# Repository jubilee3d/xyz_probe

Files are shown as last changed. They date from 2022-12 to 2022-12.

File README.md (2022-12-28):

# Jubilee XYZ Probe Tool
A touch probe for various measurement applications

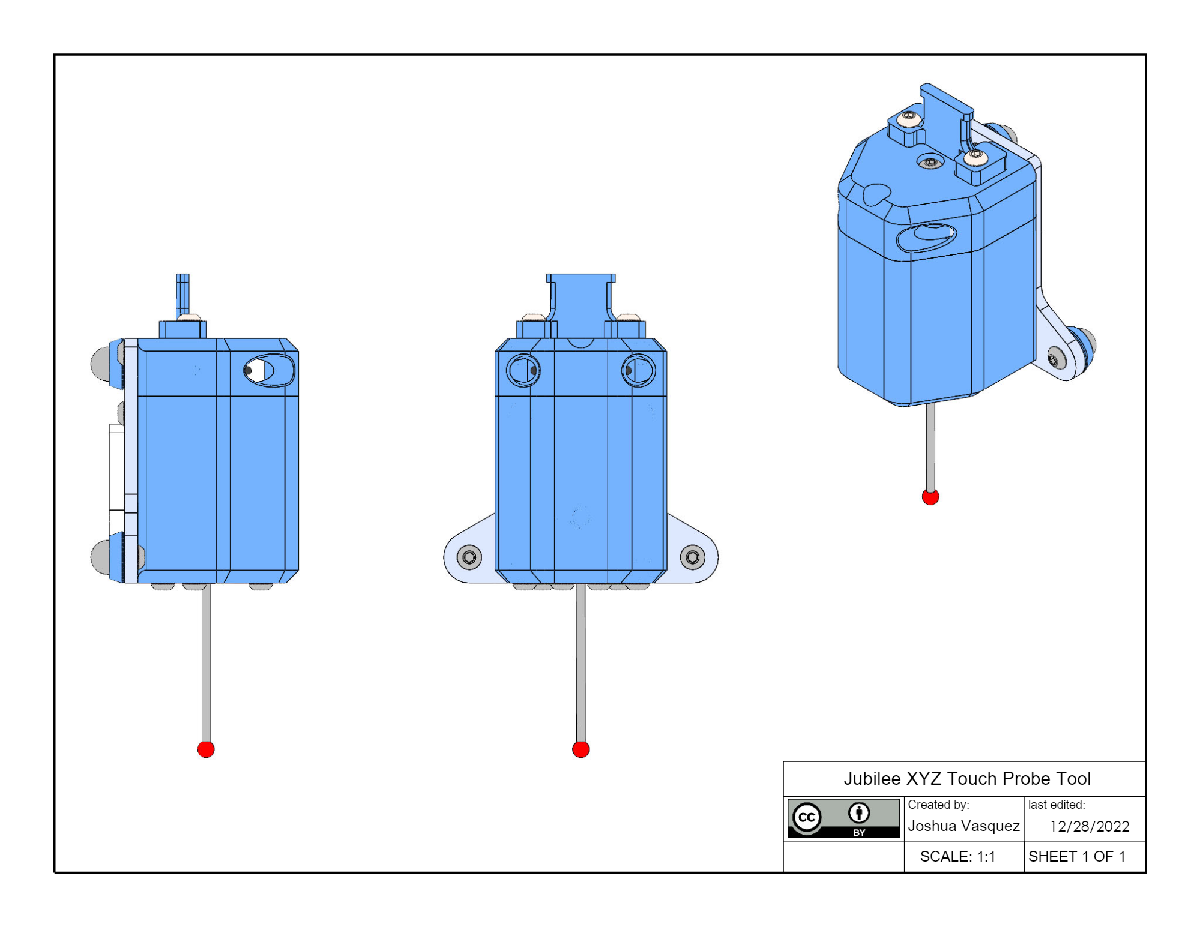
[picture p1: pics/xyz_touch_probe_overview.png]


## Overview
This is a Jubilee-compatible XYZ Probe.
It can act as a replacement for the existing z-limit switch or as a general means of inspecting items on the bed.
Probing gives the machine the ability to register against arbitrary features on the bed, enabling the possibility of resuming partial prints, scanning objects, or inspecting the existing dimensions of objects.

The XYZ probe can be reproduced from both printed and stock parts with a single unit costing about $50.
Simply order the parts in the [Shopping List](https://docs.google.com/spreadsheets/d/1exzQQtGWq62kmWazMUU2xbrfU62XK9QZYXhOB--K8R0/edit?usp=sharing) and follow the step-by-step instructions.

For more information on provisioning this tool for Jubilee, have a look at its corresponding [tool page](https://jubilee3d.com/index.php?title=XYZ_Probe_Tool).

## Specs
* probe the full XY volume. Probe *into* pockets up to 38 [mm] deep.
* compact! Does not sacrifice any of the build volume.
* Purchased Parts called out in the [Shopping List]()

## Community
This tool is part of the bigger ecosystem of Jubilee-compatible tools that implement the [E3D Toolchanger Coupler](https://github.com/e3donline/ToolChanger) standard.
For more on Jubilee, have a look at the [parent project](https://github.com/machineagency/jubilee) or join the [Discord](https://discord.gg/jubilee).

## Who made this?
This tool was created by [Joshua Vasquez](http://www.doublejumpelectric.com/) formerly at [Machine Agency](http://depts.washington.edu/machines/) at the University of Washington.

## Use the Source!
This tool is licensed with a [Creative Commons Attribution 4.0 Unported License](https://creativecommons.org/licenses/by/4.0/).

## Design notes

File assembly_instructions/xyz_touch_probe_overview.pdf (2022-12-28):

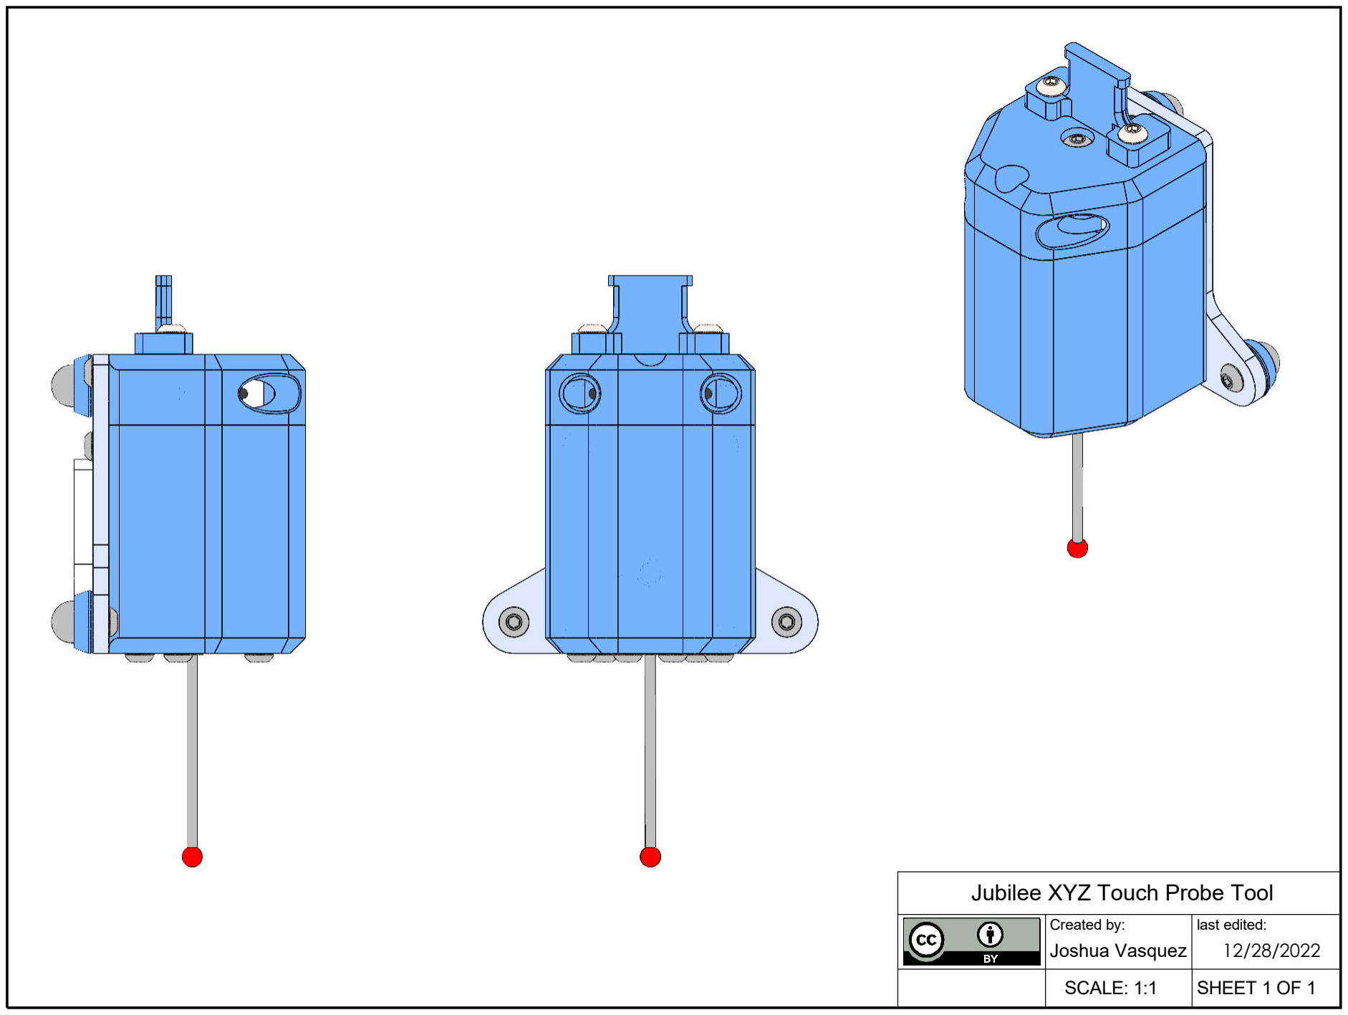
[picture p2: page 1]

12/28/2022

SHEET 1 OF 1

last edited:

SCALE: 1:1

Joshua Vasquez

Created by:

### Jubilee XYZ Touch Probe Tool

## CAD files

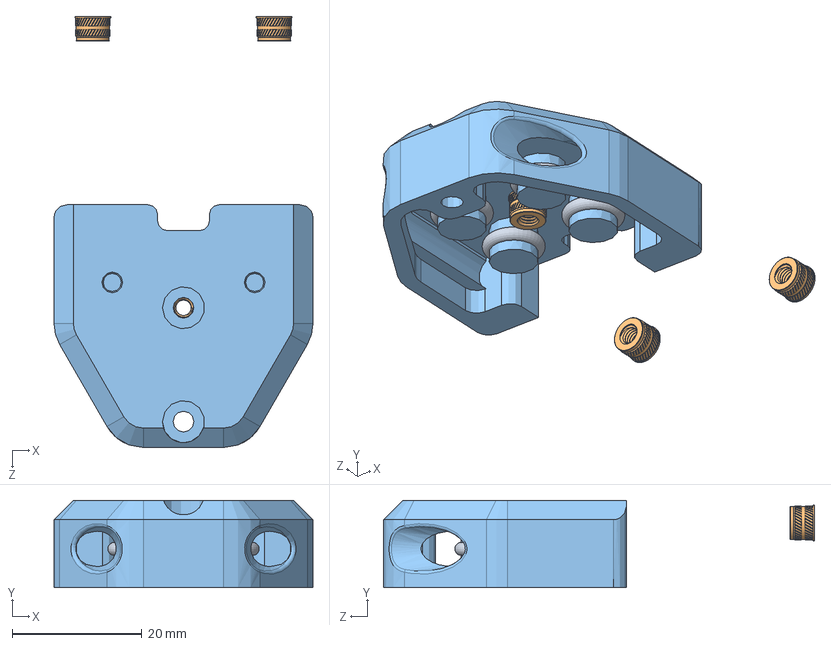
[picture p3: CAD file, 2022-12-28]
cads/solidworks/lid_assembly.SLDASM
40.0 x 13.5 x 66.6 mm
5x9x2_oring x 4
m3_heat_set_insert_94180A331 x 3
housing

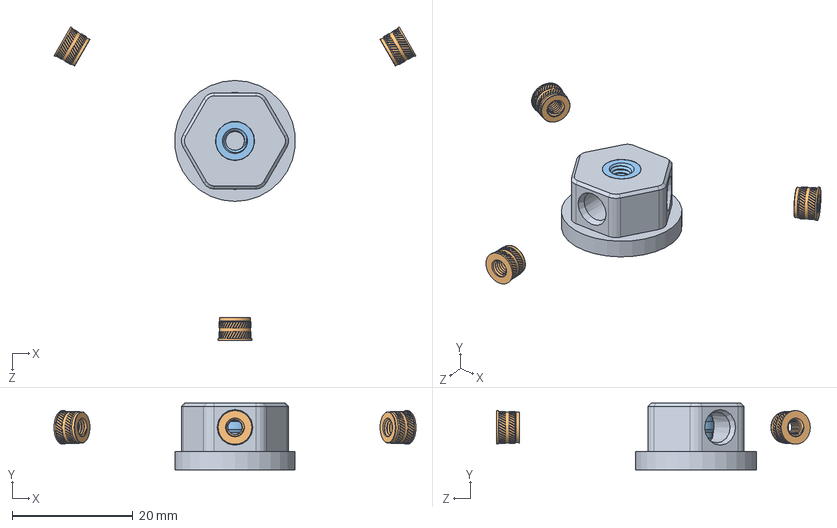
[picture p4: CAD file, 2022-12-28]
cads/solidworks/coupling_junction.SLDASM
59.8 x 11.0 x 51.8 mm
touch_probe_coupling_joint
m3_heat_set_insert_94180A331 x 3
m4_heat_set_insert_long_94180A353

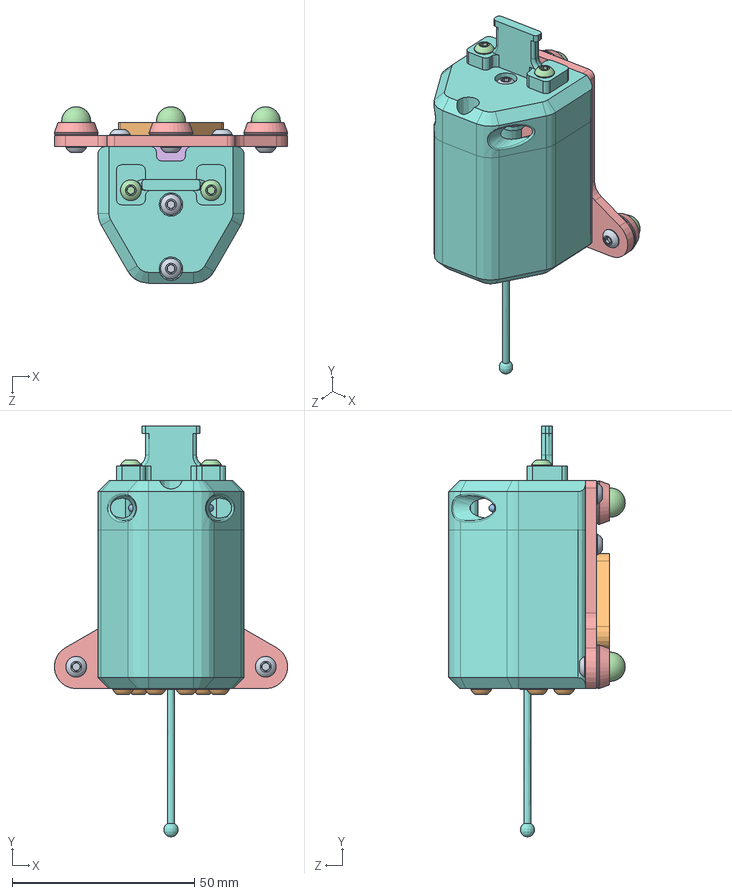
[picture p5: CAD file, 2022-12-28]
cads/solidworks/touch_probe_v2.SLDASM
64.0 x 112.7 x 48.4 mm
m3_6mm_buttonhead_screw_92095A179 x 11
wedge_plate
m3_6mm_flathead_screw_92125A126 x 3
m3_threaded_ball x 3
metal_base_tool_plate x 4
pcb
m3_8mm_threaded_ball x 6
housing x 4
m3_heat_set_insert_94180A331 x 11
m3_12mm_buttohead_screw_92095A183 x 6
5x9x2_oring x 4
m3_8mm_buttonhead_screw_92095A181 x 2
touch_probe_coupling_joint
m4_heat_set_insert_long_94180A353
m3_shoulder_screw_4mm_d_8mm_l_94128A105 x 3
probe

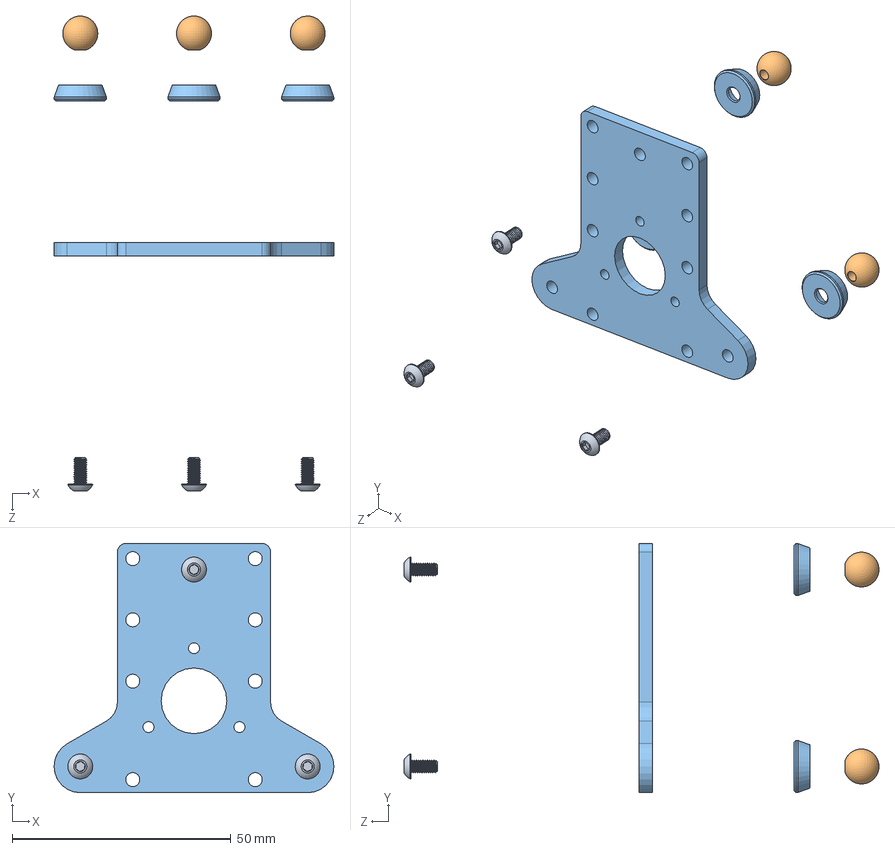
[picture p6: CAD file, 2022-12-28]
cads/solidworks/base_tool_plate_assembly.SLDASM
64.0 x 57.0 x 108.6 mm
m3_6mm_buttonhead_screw_92095A179 x 3
m3_threaded_ball x 3
metal_base_tool_plate x 4

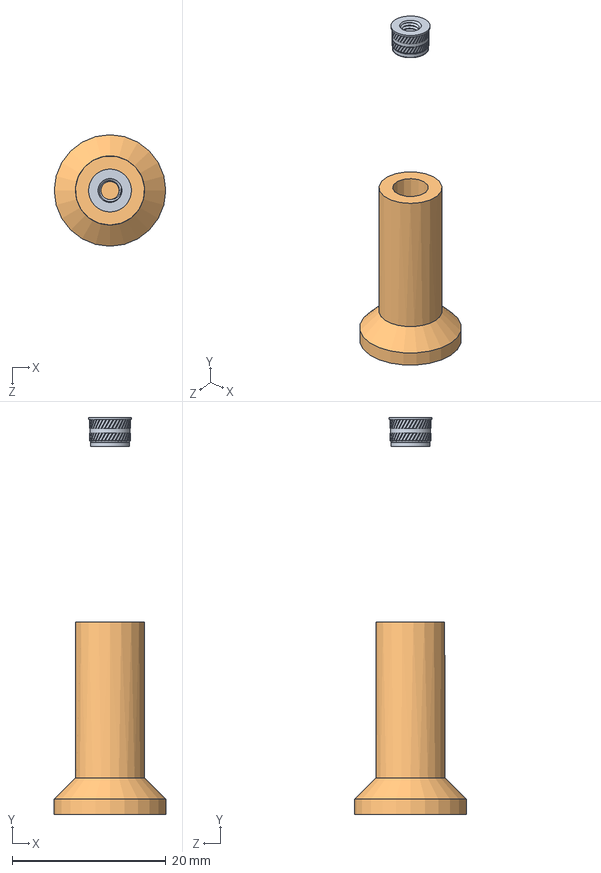
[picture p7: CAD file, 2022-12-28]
cads/solidworks/spring_preload_stud.SLDASM
14.5 x 51.6 x 14.5 mm
m3_heat_set_insert_94180A331
housing

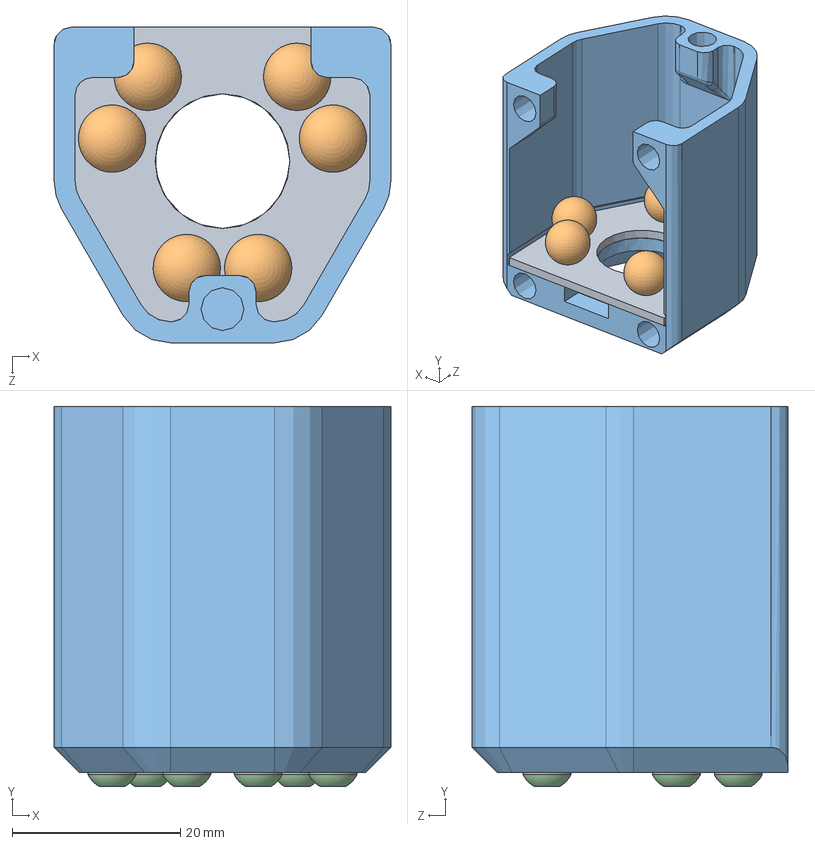
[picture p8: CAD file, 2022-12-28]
cads/solidworks/base_with_tool_balls.SLDASM
40.0 x 45.2 x 37.5 mm
pcb
m3_8mm_threaded_ball x 6
housing
m3_12mm_buttohead_screw_92095A183 x 6

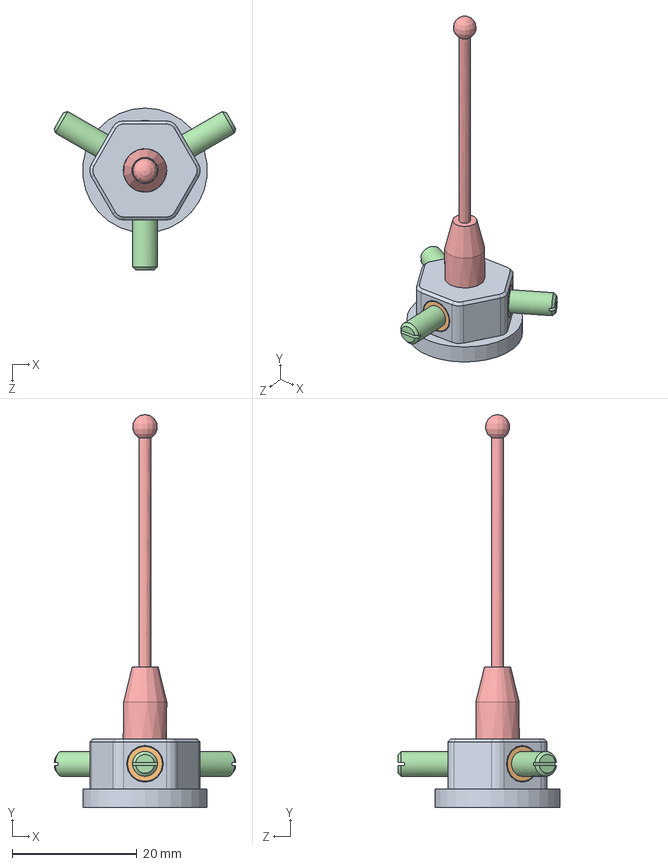
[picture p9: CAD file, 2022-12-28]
cads/solidworks/probe_tip.SLDASM
29.1 x 63.0 x 26.0 mm
touch_probe_coupling_joint
m3_heat_set_insert_94180A331 x 3
m4_heat_set_insert_long_94180A353
m3_shoulder_screw_4mm_d_8mm_l_94128A105 x 3
probe

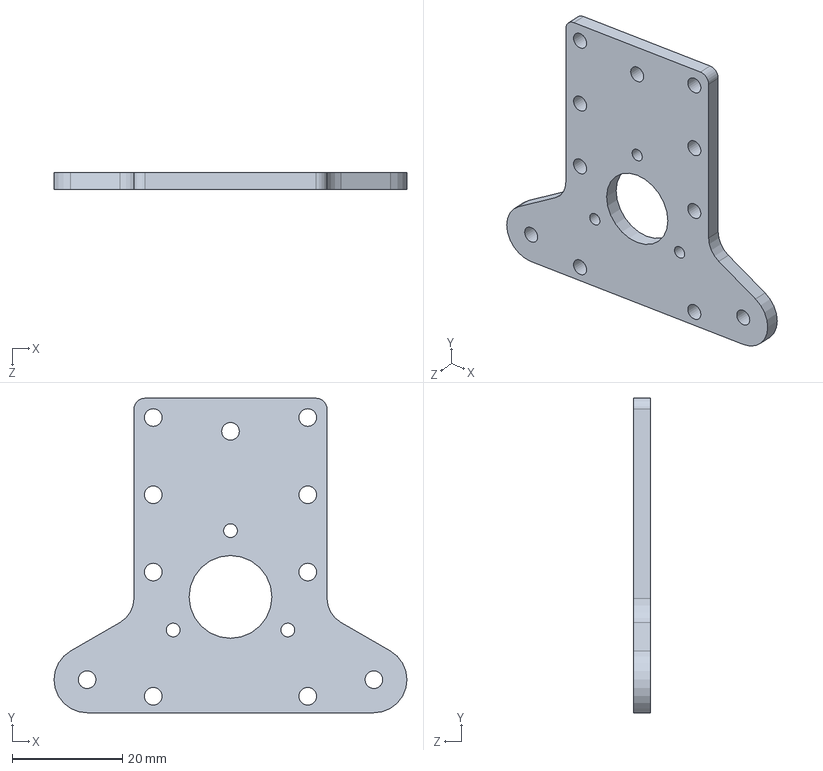
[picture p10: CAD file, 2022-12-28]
cads/solidworks/metal_base_tool_plate.SLDPRT
64.0 x 57.0 x 3.00 mm

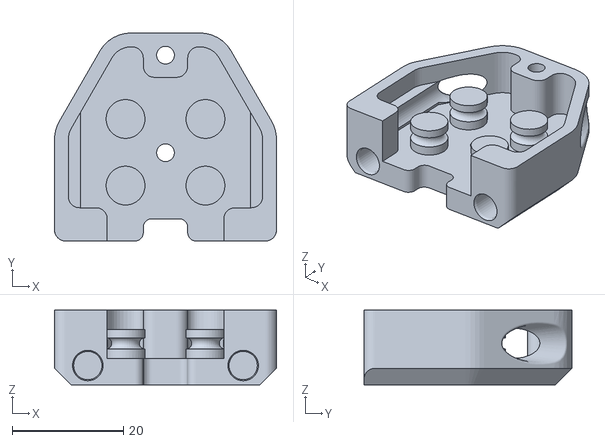
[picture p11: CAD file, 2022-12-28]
fabrication_exports/printed_lid.STL
40.0 x 37.5 x 13.5

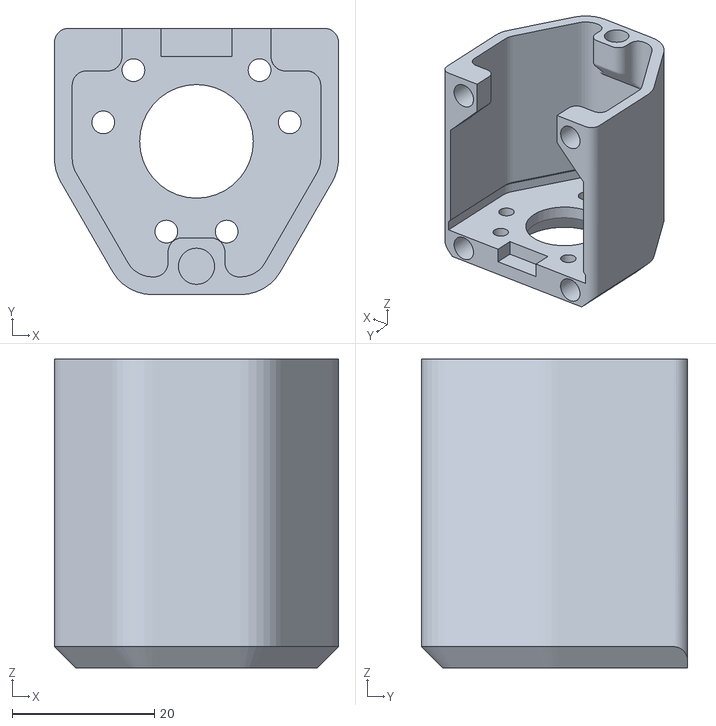
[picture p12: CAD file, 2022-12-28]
fabrication_exports/printed_base.STL
40.0 x 37.5 x 43.5

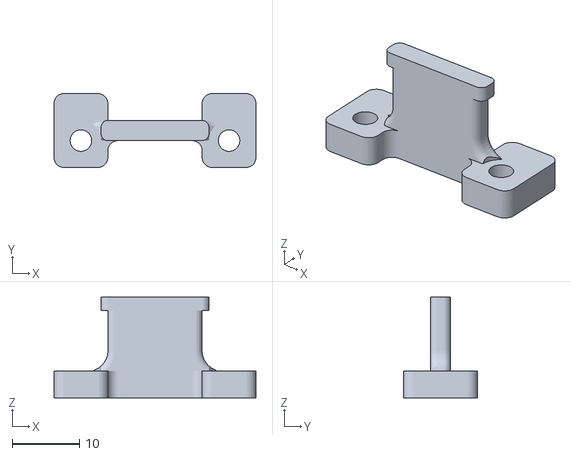
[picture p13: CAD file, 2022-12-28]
fabrication_exports/printed_wire_tab.STL
30.0 x 11.0 x 15.0

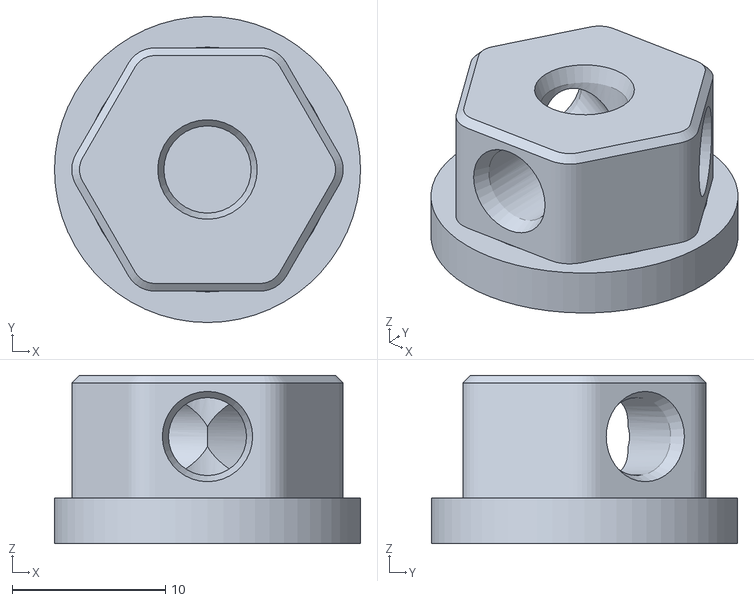
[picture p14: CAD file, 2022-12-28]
fabrication_exports/coupling_junction.STL
20.0 x 20.0 x 11.0

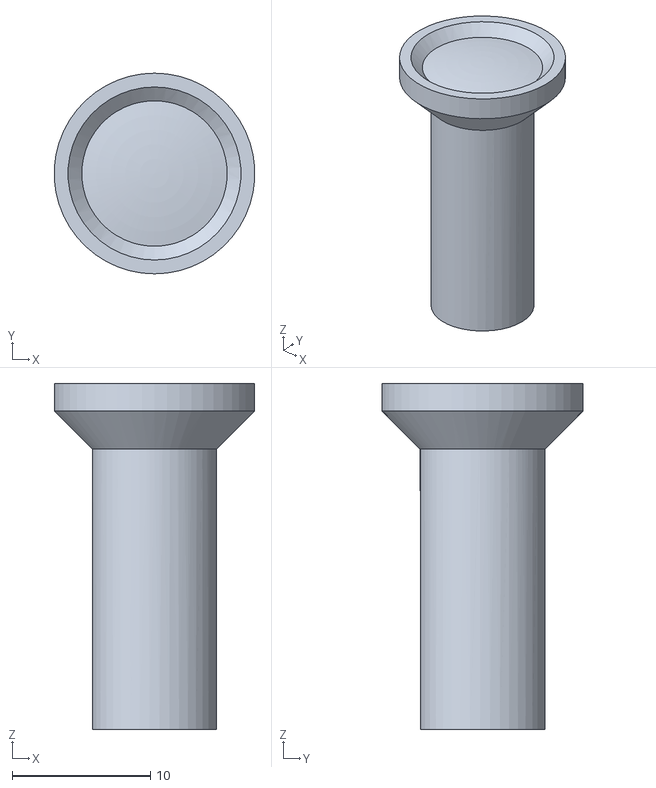
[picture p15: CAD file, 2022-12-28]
fabrication_exports/printed_spring_stud.STL
14.5 x 14.5 x 25.0

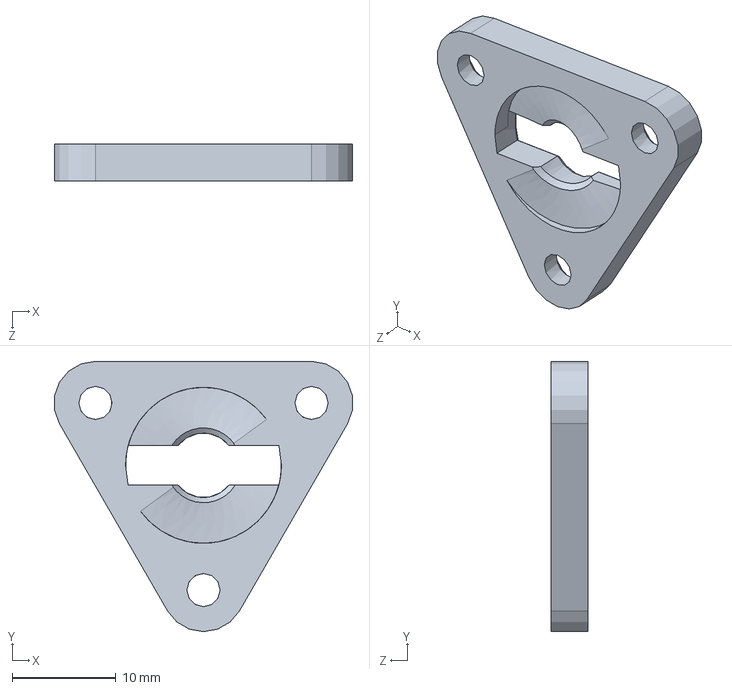
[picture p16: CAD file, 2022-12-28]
cads/solidworks/wedge_plate.SLDPRT
28.7 x 26.0 x 3.60 mm

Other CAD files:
fabrication_exports/tool_ball_cup.STL
cads/solidworks/pcb.SLDPRT
cads/solidworks/m3_threaded_ball.SLDPRT
cads/solidworks/probe.SLDPRT
cads/solidworks/5x9x2_oring.SLDPRT
cads/solidworks/housing.SLDPRT
cads/solidworks/m3_12mm_buttohead_screw_92095A183.SLDPRT
cads/solidworks/m3_6mm_buttonhead_screw_92095A179.SLDPRT
cads/solidworks/m3_6mm_flathead_screw_92125A126.SLDPRT
cads/solidworks/m3_8mm_buttonhead_screw_92095A181.SLDPRT
cads/solidworks/m3_8mm_threaded_ball.SLDPRT
cads/solidworks/m3_heat_set_insert_94180A331.SLDPRT
cads/solidworks/m3_shoulder_screw_4mm_d_8mm_l_94128A105.SLDPRT
cads/solidworks/m4_heat_set_insert_long_94180A353.SLDPRT
cads/solidworks/touch_probe_coupling_joint.SLDPRT

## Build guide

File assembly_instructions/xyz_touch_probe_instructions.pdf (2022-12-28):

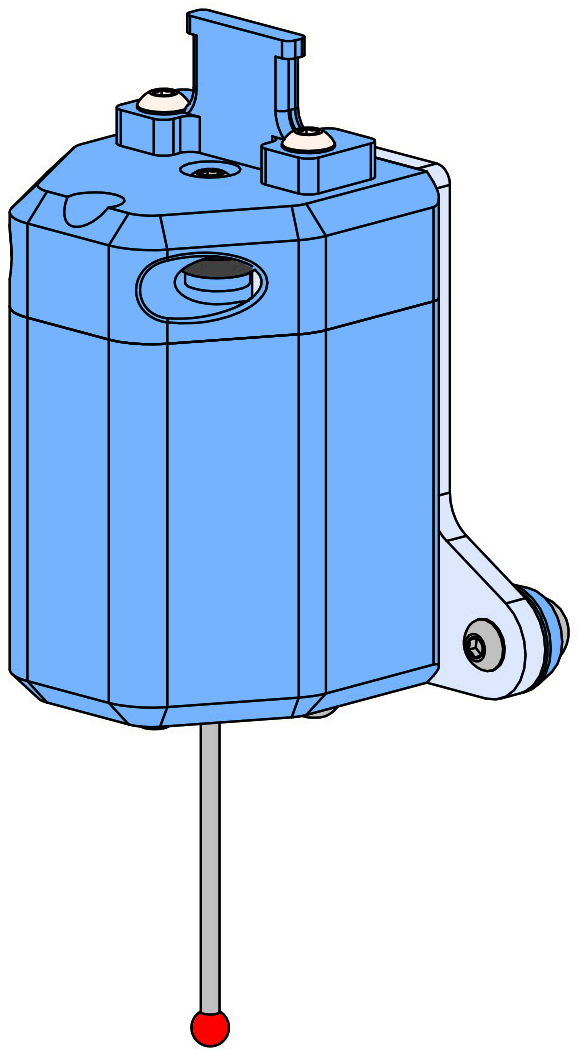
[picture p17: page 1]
SCALE: 1:5; SHEET 1 OF 11; Joshua Vasquez; Created by:; last edited:

XYZ Touch Probe

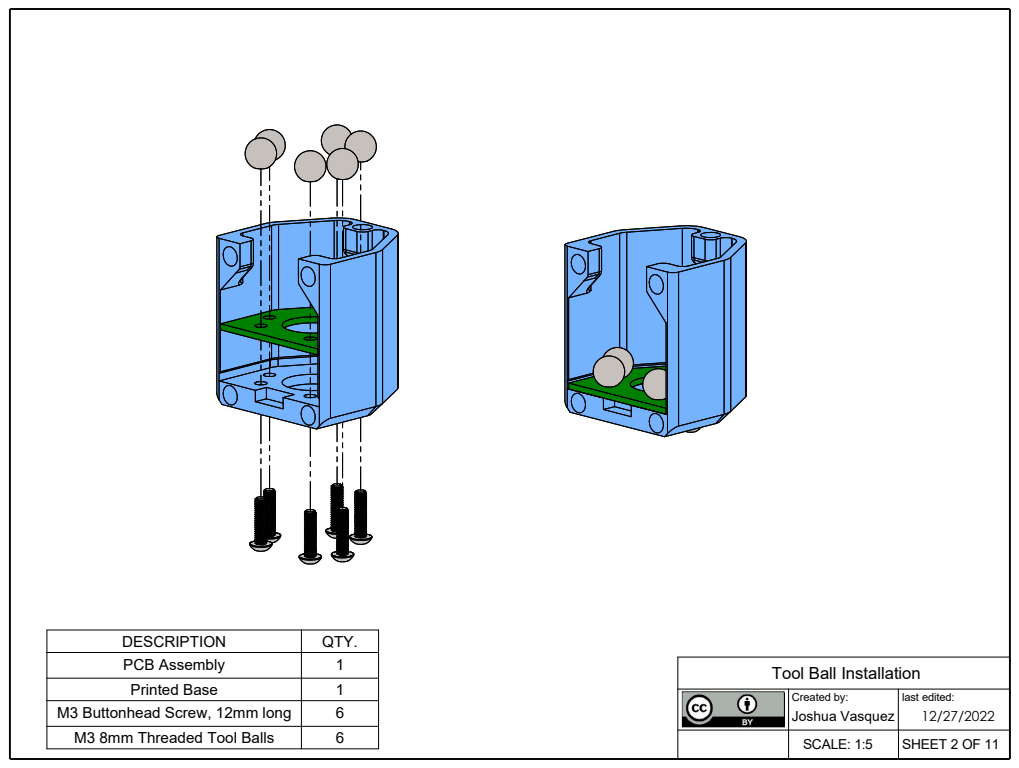
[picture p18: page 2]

DESCRIPTION | QTY.
PCB Assembly | 1
Printed Base | 1

Tool Ball Installation

Created by: Joshua Vasquez | last edited: 12/27/2022

M3 Buttonhead Screw, 12mm long | 6
M3 8mm Threaded Tool Balls | 6

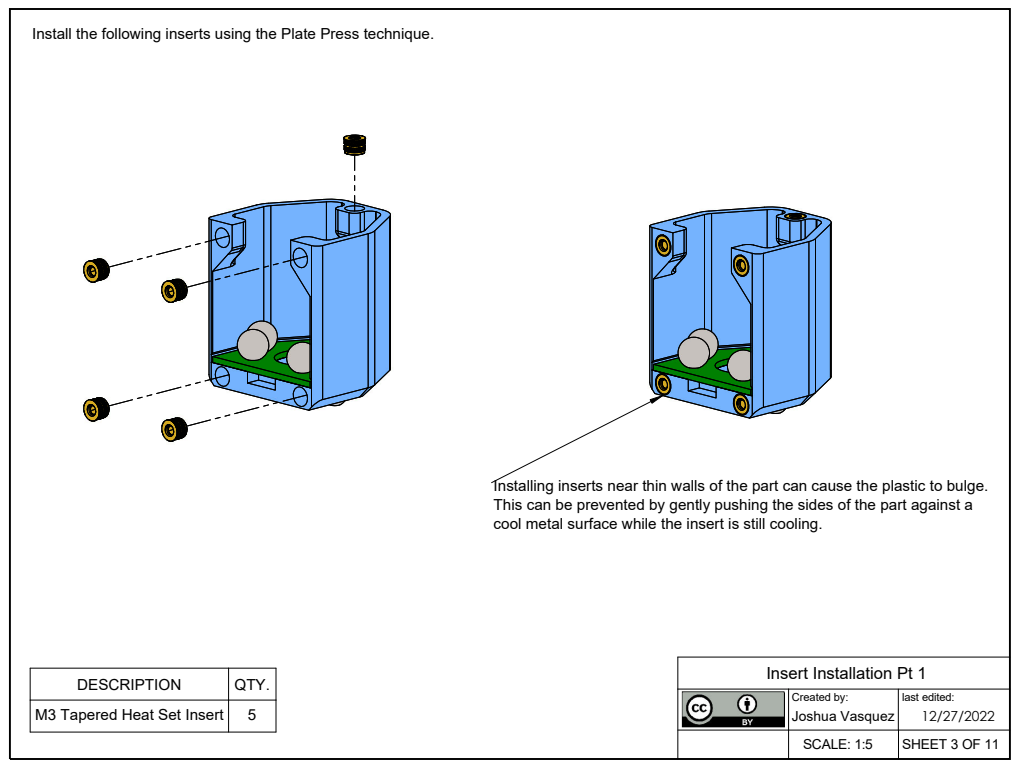
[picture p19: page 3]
Joshua Vasquez; Created by:; last edited:; Insert Installation Pt 1 DESCRIPTION; QTY.; M3 Tapered Heat Set Insert

Install the following inserts using the Plate Press technique.

Installing inserts near thin walls of the part can cause the plastic to bulge.
This can be prevented by gently pushing the sides of the part against a
cool metal surface while the insert is still cooling.

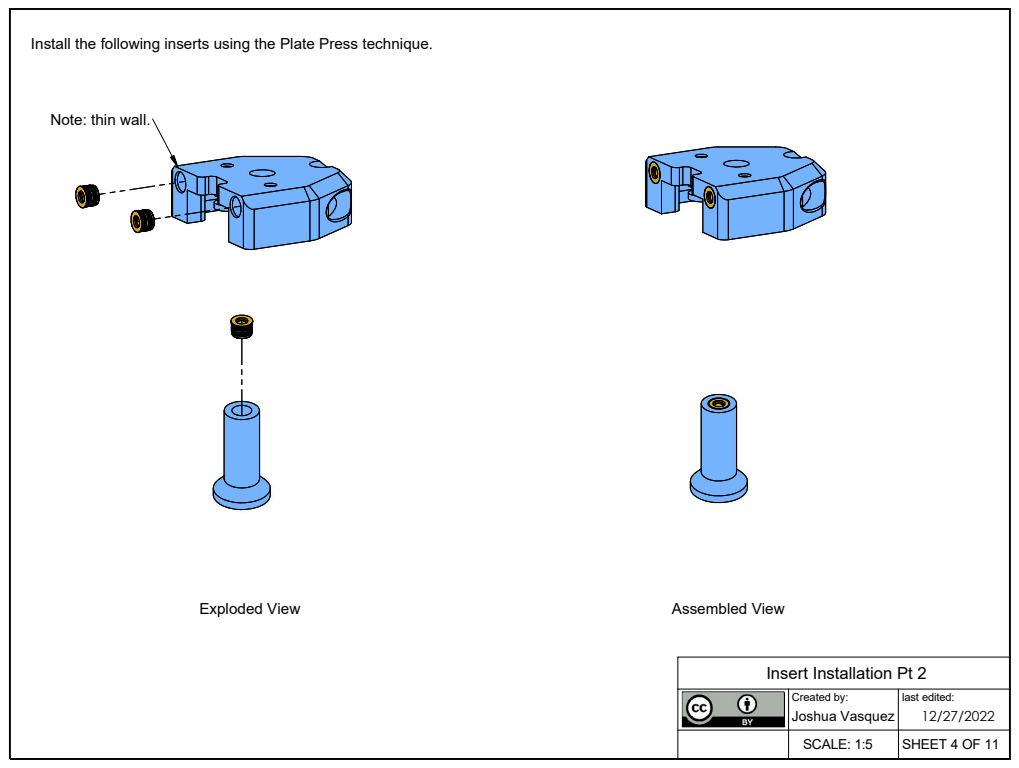
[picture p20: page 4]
Joshua Vasquez; Created by:; last edited:; Exploded View; Assembled View

Install the following inserts using the Plate Press technique.

Note: thin wall.

Insert Installation Pt 2

1 | 2

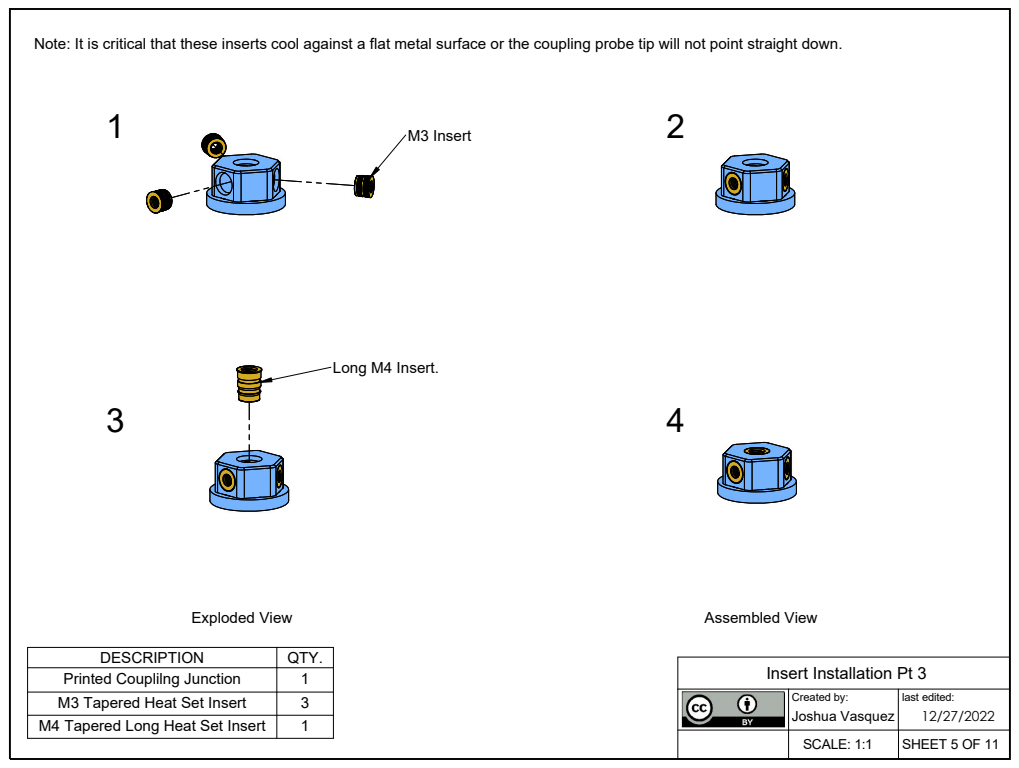
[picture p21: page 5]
SCALE: 1:1; SHEET 5 OF 11; Joshua Vasquez; Created by:; last edited:; Exploded View; Assembled View; M3 Insert; Long M4 Insert.

Note: It is critical that these inserts cool against a flat metal surface or the coupling probe tip will not point straight down.

DESCRIPTION | QTY.
Printed Couplilng Junction | 1
M3 Tapered Heat Set Insert | 3
M4 Tapered Long Heat Set Insert | 1

Insert Installation Pt 3

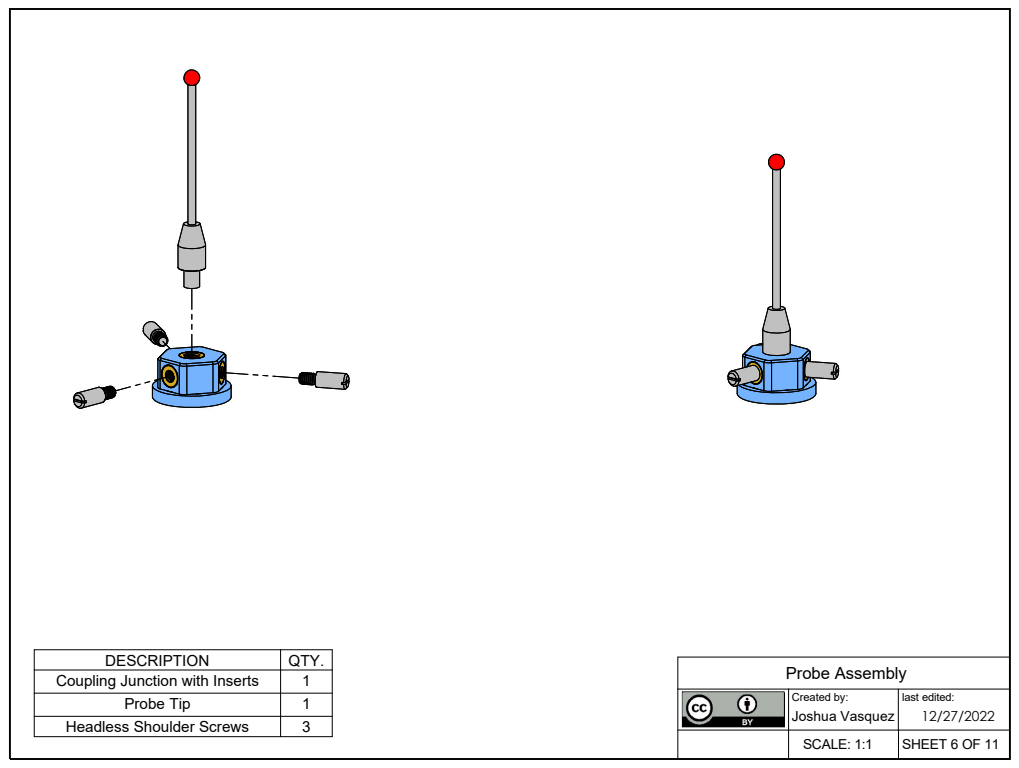
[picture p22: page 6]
SCALE: 1:1; SHEET 6 OF 11; Joshua Vasquez; Created by:; last edited:; Probe Assembly

DESCRIPTION | QTY.
Coupling Junction with Inserts | 1

Probe Tip | 1

Headless Shoulder Screws | 3

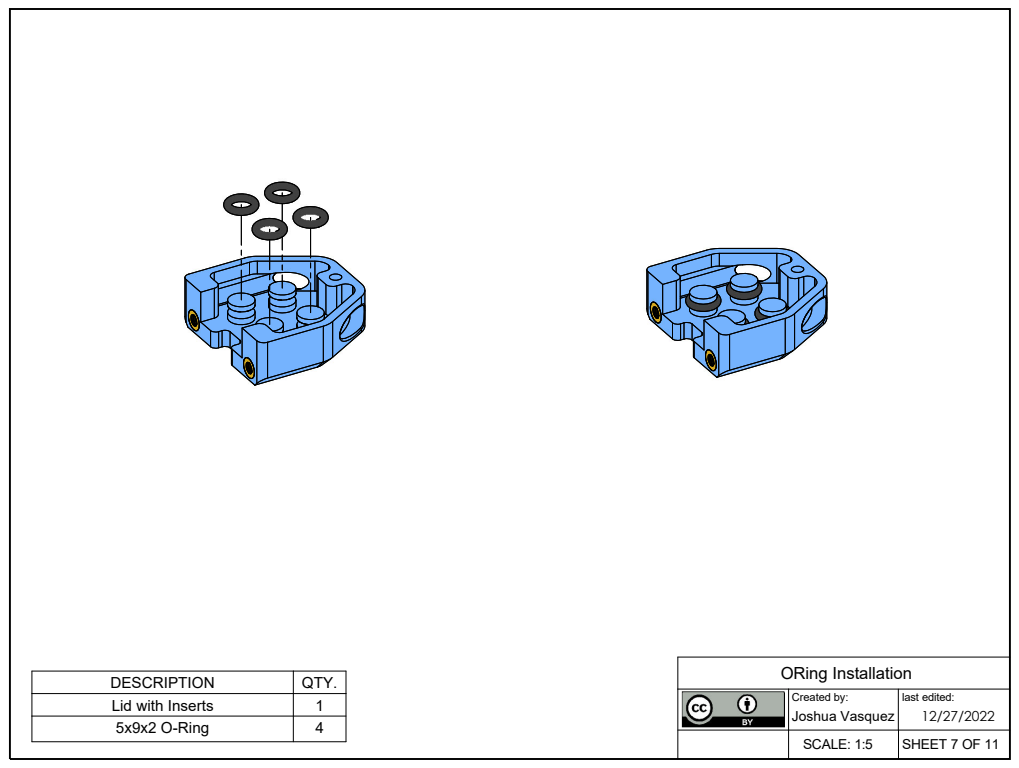
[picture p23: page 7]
Joshua Vasquez; Created by:; last edited:; ORing Installation DESCRIPTION; QTY.

Lid with Inserts | 1
5x9x2 O-Ring | 4

7

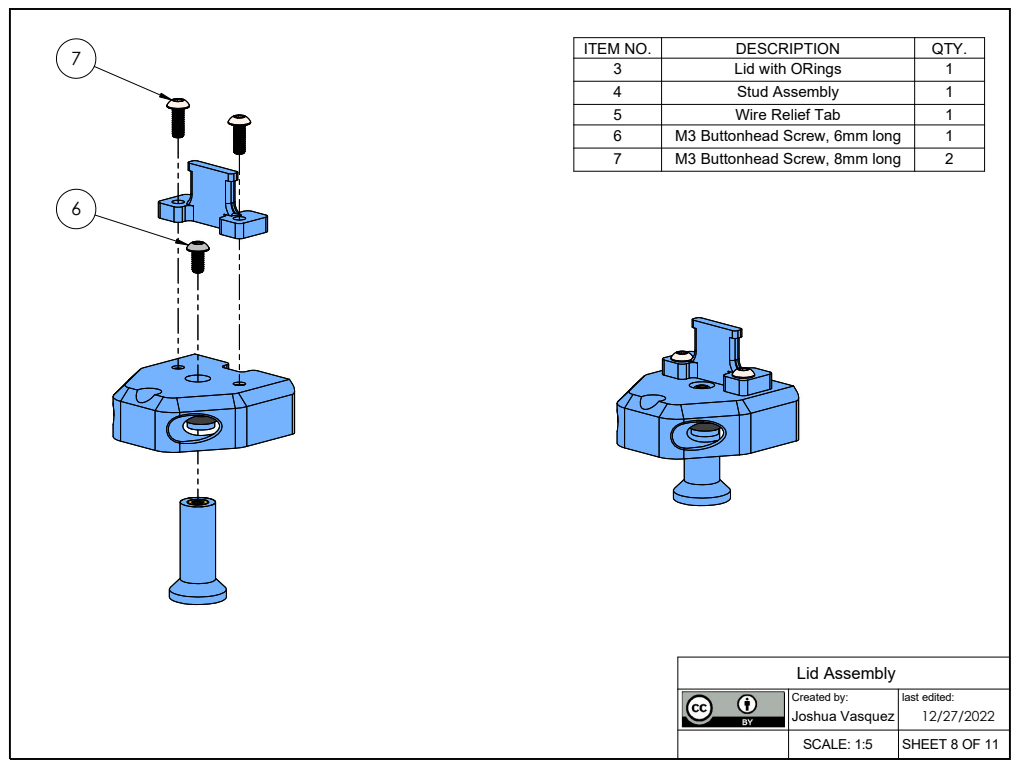
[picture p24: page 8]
Joshua Vasquez; Created by:; last edited:; Lid Assembly

ITEM NO. | DESCRIPTION | QTY.
3 | Lid with ORings | 1
4 | Stud Assembly | 1
5 | Wire Relief Tab | 1
6 | M3 Buttonhead Screw, 6mm long | 1
7 | M3 Buttonhead Screw, 8mm long | 2

1 | 2

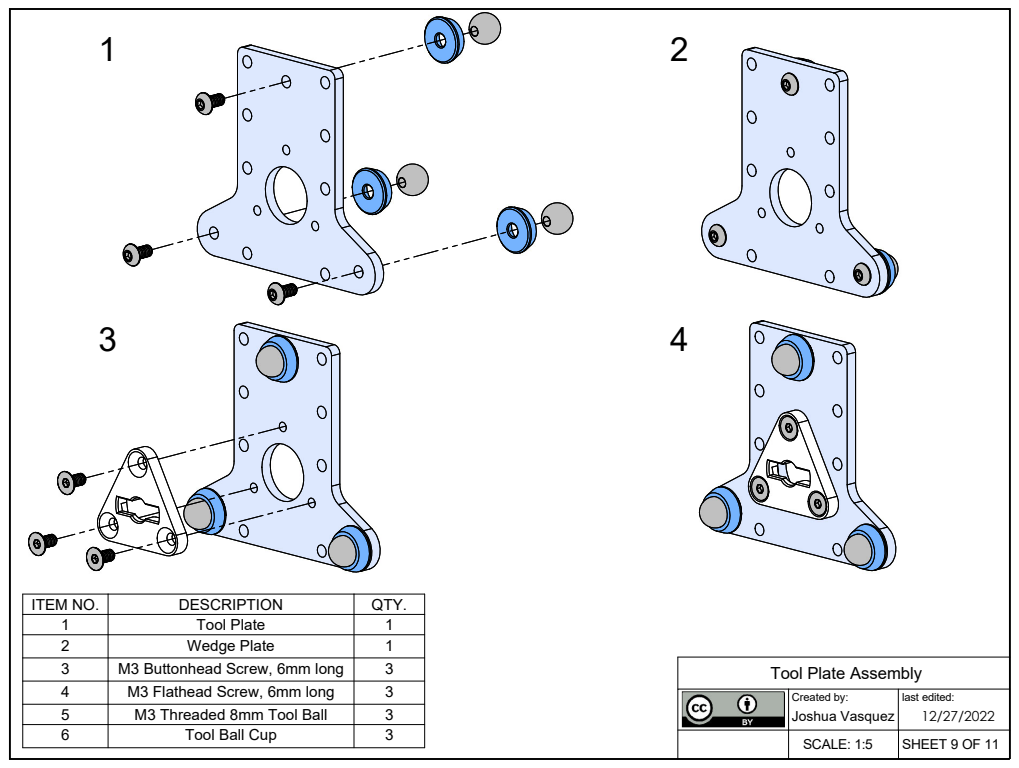
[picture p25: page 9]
Joshua Vasquez; Created by:; last edited:

ITEM NO. | DESCRIPTION | QTY.
1 | Tool Plate | 1
2 | Wedge Plate | 1
3 | M3 Buttonhead Screw, 6mm long | 3
4 | M3 Flathead Screw, 6mm long | 3
5 | M3 Threaded 8mm Tool Ball | 3
6 | Tool Ball Cup | 3

Tool Plate Assembly

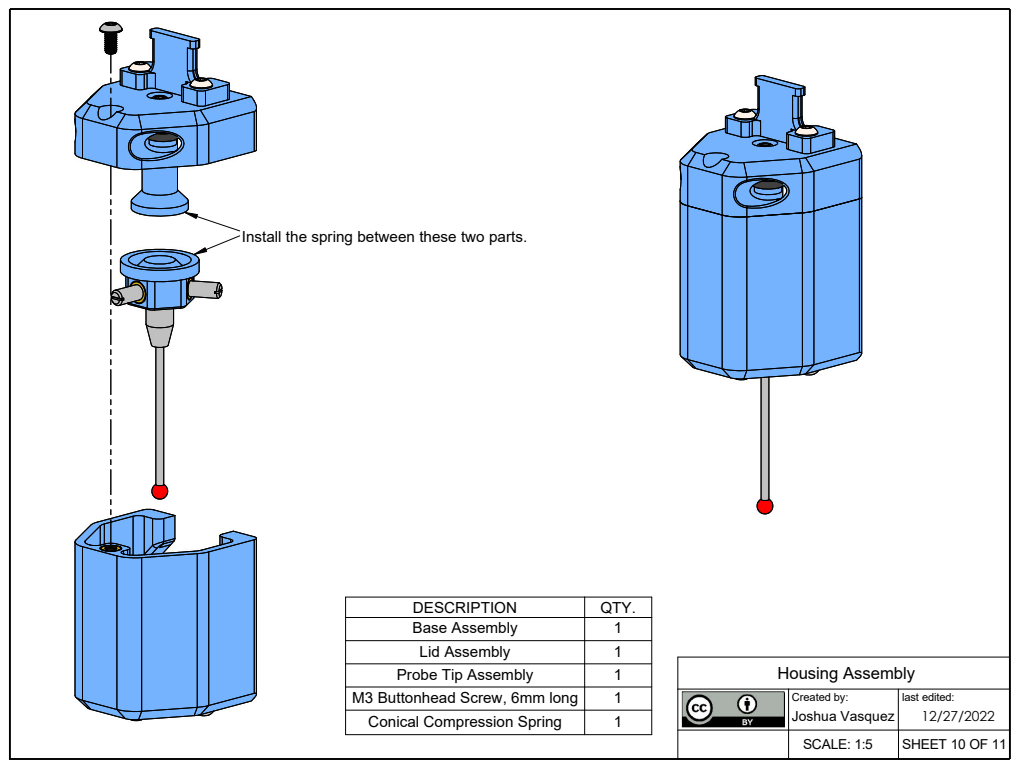
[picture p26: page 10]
Joshua Vasquez; Created by:; last edited:; Housing Assembly; M3 Buttonhead Screw, 6mm long; Conical Compression Spring

Install the spring between these two parts.

DESCRIPTION | QTY.
Base Assembly | 1
Lid Assembly | 1
Probe Tip Assembly | 1

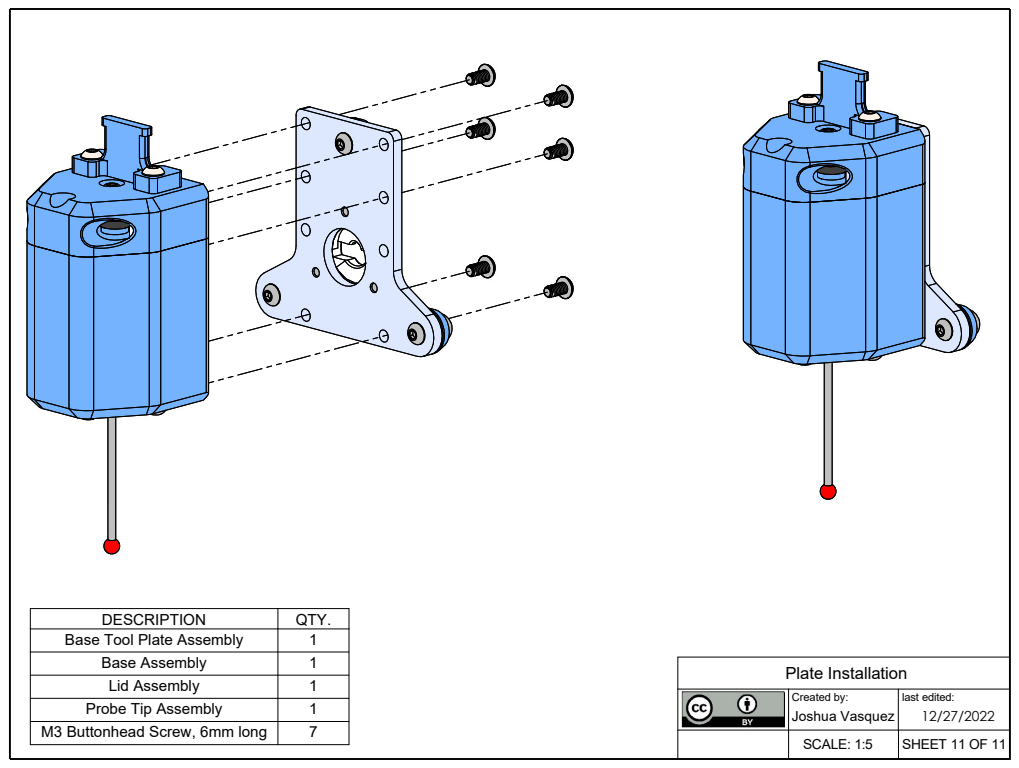
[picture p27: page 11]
Joshua Vasquez; Created by:; last edited:; Plate Installation

DESCRIPTION | QTY.
Base Tool Plate Assembly | 1
Base Assembly | 1
Lid Assembly | 1
Probe Tip Assembly | 1
M3 Buttonhead Screw, 6mm long | 7

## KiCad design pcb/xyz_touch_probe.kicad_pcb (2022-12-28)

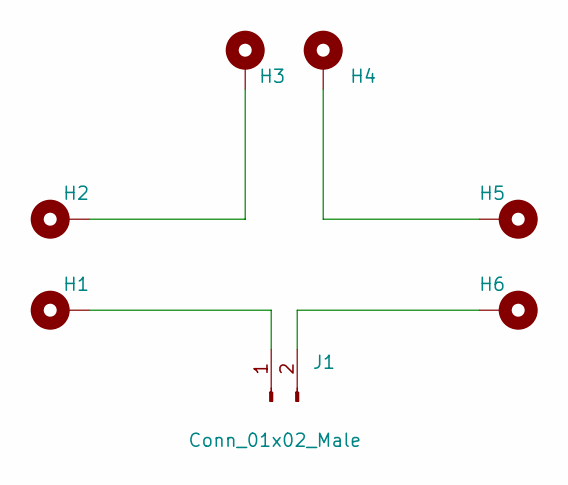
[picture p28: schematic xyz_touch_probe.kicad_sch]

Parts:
H1, H2, H3, H4, H5, H6: MountingHole_Pad; MountingHole_3.2mm_M3_DIN965_Pad
J1: Conn_01x02_Male; PinHeader_1x02_P2.54mm_Vertical

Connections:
unnamed: H1.1, J1.1
unnamed: H2.1, H3.1
unnamed: H4.1, H5.1
unnamed: H6.1, J1.2

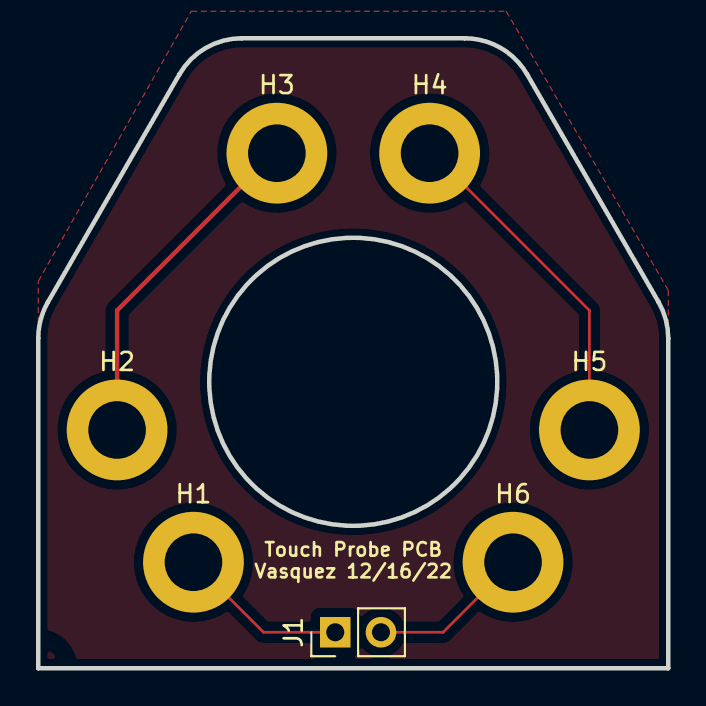
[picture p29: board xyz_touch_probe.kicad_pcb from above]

Board: 2 copper layers, 35.0 x 35.0 mm, 7 parts (0 on the bottom side), 4 nets.
